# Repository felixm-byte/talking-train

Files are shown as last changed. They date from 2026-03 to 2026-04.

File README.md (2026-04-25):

# talking-train
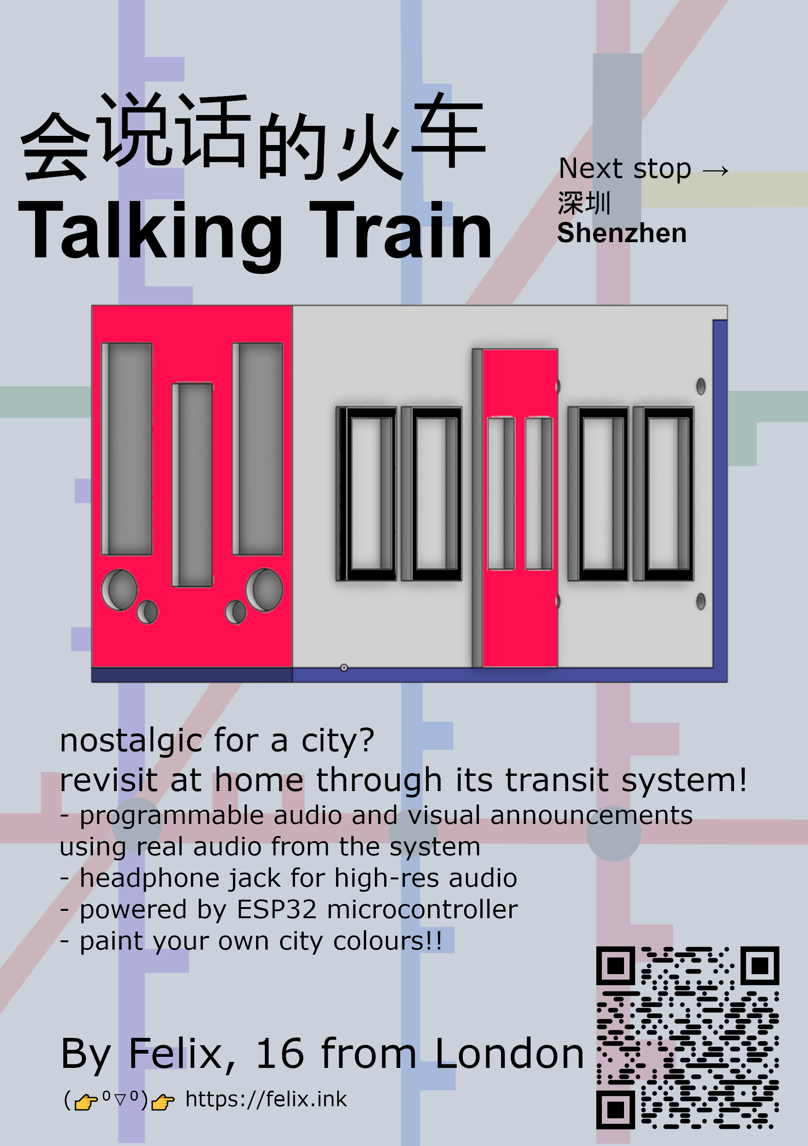
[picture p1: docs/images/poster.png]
poster describing features of the talking train, with a features list and 3D model resembling a London Underground train


This is a bit of an odd concept, but I want to make a talking model train for my grandparents to remind them of their times visiting us, since they are too old to ever make the 19,000 km journey from New Zealand to England. Every time I call them from the train, they light up at the familiarity of the announcements when they hear them and get super nostalgic, which makes me think it would be nice—and a cool souvenir—to let them hear them whenever they like. Technically, I think it would be a cool project, since I’ve never made something with a physical interface, or really made something with hardware, and I would love to learn. Most of what I build would be applicable to other countries, so I think it would be something lots of people would like.

## File structure
- Please ignore /hardware/old-design, for reference only
- Manufacturing files in hardware/manufacturing-outputs/...
- Code in /software - these scripts are in MicroPython and target the ESP32 microcontroller, expecting a 128x64 SSD1306 I2C OLED display and an [I2S audio output device](https://github.com/miketeachman/micropython-i2s-examples)
## Part examples
- SSD1306 128x64 display: https://www.aliexpress.com/item/1005007551771400.html
- Check Bill of Materials file for all other parts, these have LSCS part numbers for ease of ordering
- 4x M2 screws with nuts, 1.4cm length - https://www.aliexpress.com/item/1005006328031034.html (M2x14mm needed)

## Features
- Loads stations and displays them in order on the OLED screen
- Audio playback with hi-res audio
- Line creation tool
- Audio playback support

## Key files
- hardware/manufacturing-outputs/ contains the files (.stl, pick and place, gerber, BOM) needed to produce the finished product, with the 3D files for the case in manufacturing-outputs/3d/ and the PCB in manufacturing-outputs/pcb/ 
- Source files like the EasyEDA (.epro) file and the 3D model of the PCB (only really necessary for designing a new case) is in hardware/source-files
- Use [the onshape file](https://cad.onshape.com/documents/c1f604bc7dcb19d0034320b9/w/e582f7a5ec8be5c9c5e2ed68/e/27ea5781da26a9e15f82bfe8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) onshape for the case 3D source, and access an interactive bom on [my website](https://felix.ink/ttrain1)
- software/ contains the line creation tool and the software for the ESP32 to run.

## Assembly
- Assemble the PCB outside of the case by soldering on the parts. Do not attach the display at this stage. 
- To protect from the unlikely event of soldering error, do not plug the usb-c port directly into an important device: plug into a wall outlet first and check if the power LED is active. If not, I recommend stopping using the device.
- Place this 3D printed piece flat on an assembly bench.
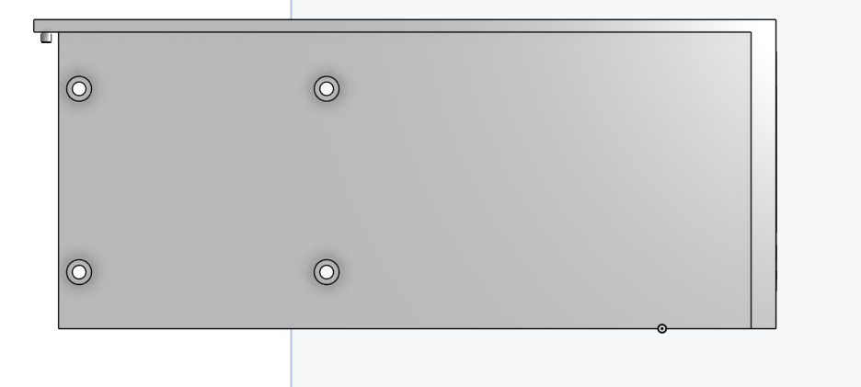
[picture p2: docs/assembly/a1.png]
part with round screw holes pointing out

- Place the PCB onto the round pieces that poke out, which are used to seperate it from the case. Make sure it is in this alignment and that the screwholes line up.
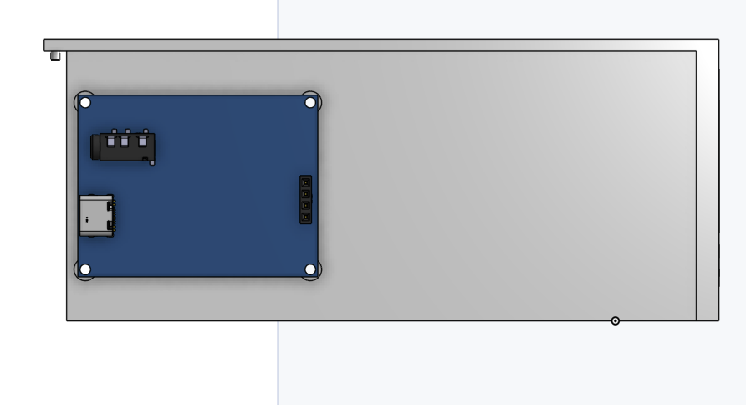
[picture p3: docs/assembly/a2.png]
PCB aligned with scewholes

- Then, insert the screws into the screwholes as shown in the graphic, taking care not to poke the board components.

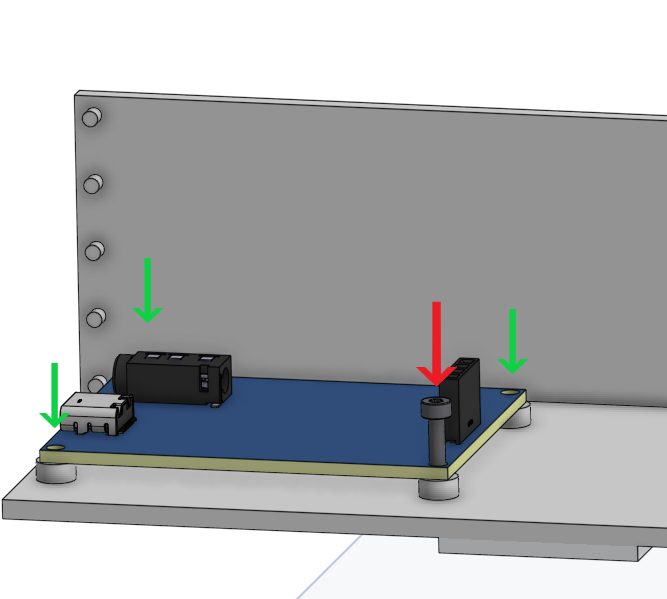
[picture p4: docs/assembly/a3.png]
Inserting screws

- Rotate the model so that it sits with the side of the train on the desk and the top of the train facing upwards. Turn the nut around the screw to secure the PCB.

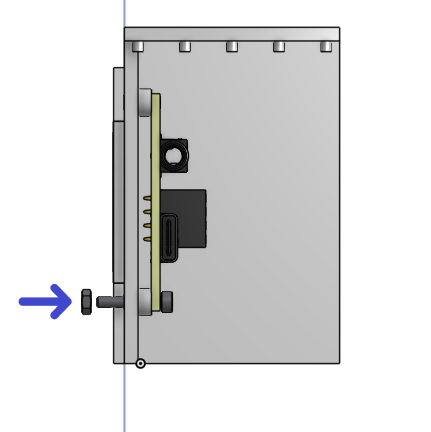
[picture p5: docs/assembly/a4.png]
Securing with nuts

- Next, return the PCB to the original orientation, with the side of the model the PCB is attached to, resting on the desk. Gently attach the display in this orientation, ensuring the pins line up with the header.

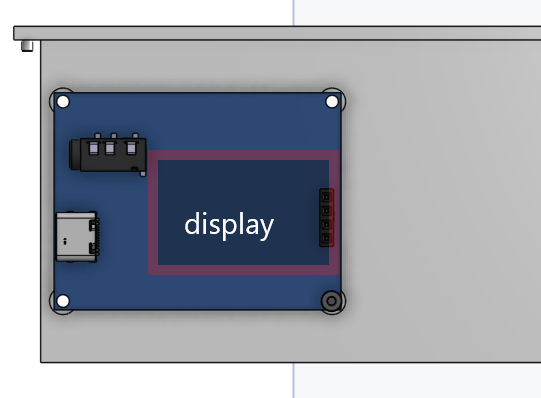
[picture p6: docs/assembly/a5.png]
Orientation for display

- Finally, take the other part of the 3D model, place it down with its base on the desk. Align the attachment pins from the top side (which we have just assembled) with the sockets from the part we put down, and push it in.

This should now be ready for use. Attach by USB-C to your computer, [set up MicroPython](https://docs.sunfounder.com/projects/esp32-starter-kit/en/latest/micropython/python_start/install_micropython.html), flash the software, and attach a pair of wired headphones to the device. 

Note: please be careful with audio - I don't know how loud it'll be until I test the model.

### For reference, other parts rendered:

The pieces used for mounting the top half of the model:
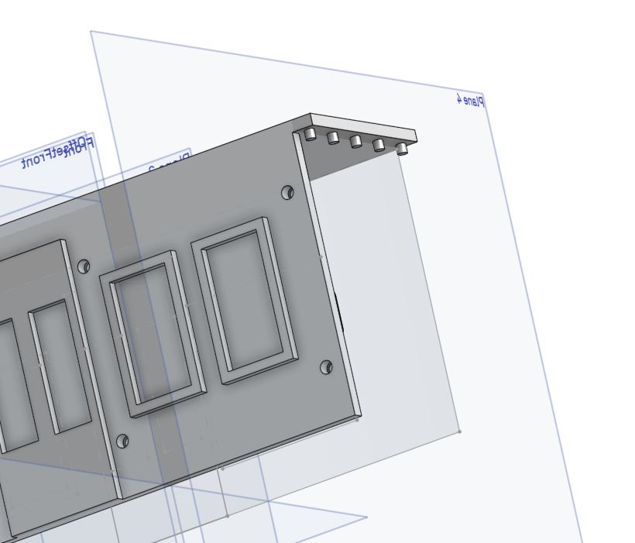
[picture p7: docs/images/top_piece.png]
render of top piece


Fit into these holes on the bottom part of the model.
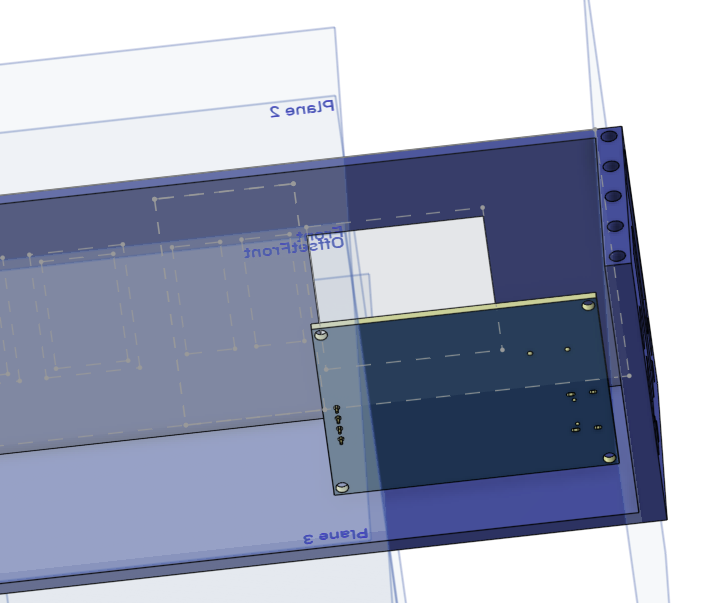
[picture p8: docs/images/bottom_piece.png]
render of bottom piece

## Graphics
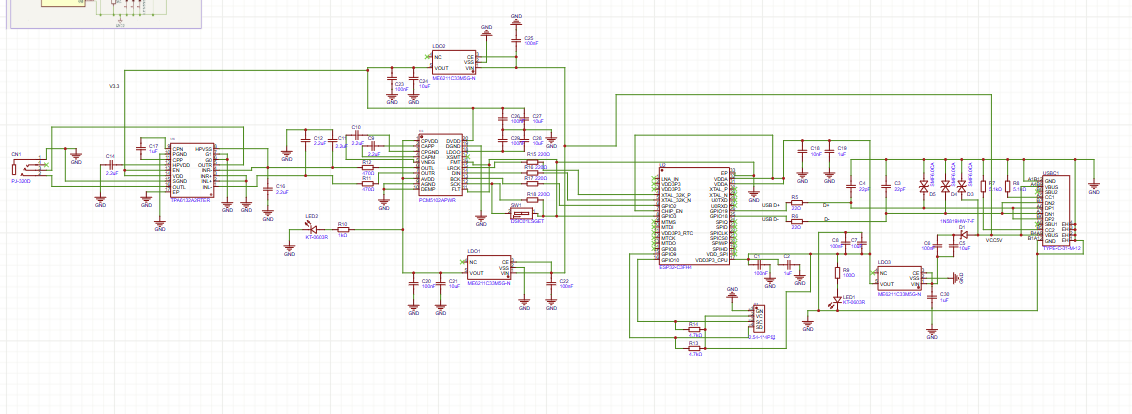
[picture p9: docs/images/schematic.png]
schematic

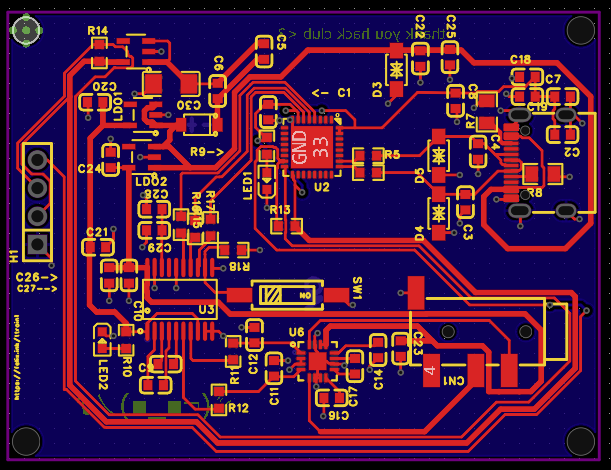
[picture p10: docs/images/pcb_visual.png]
PCB diagram (wiring)

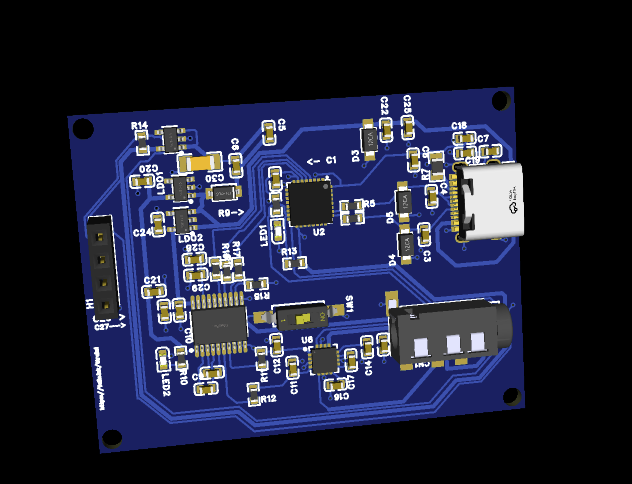
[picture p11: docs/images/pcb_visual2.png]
 - old PCB, for shape reference only
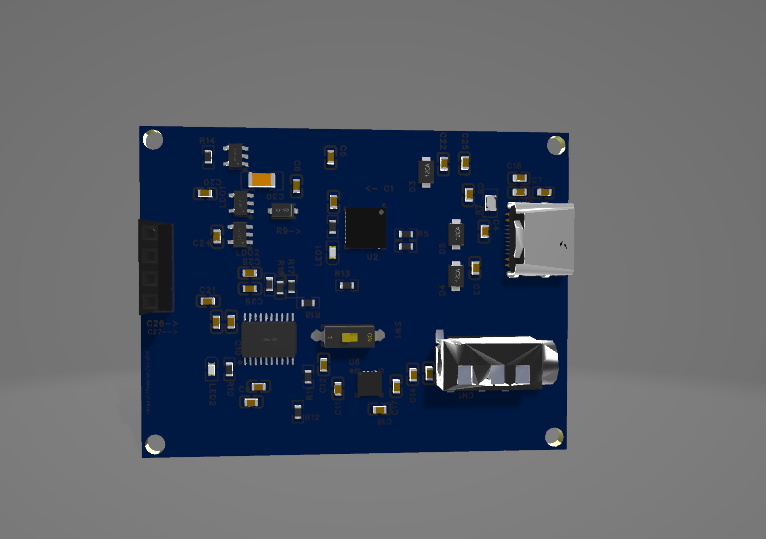
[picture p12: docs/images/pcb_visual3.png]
- old PCB, for shape reference only
## Reference materials
- https://macsbug.wordpress.com/2021/02/19/web-radio-of-m5stack-pcm5102a-i2s-dac/ for DAC schematic
- https://documentation.espressif.com/esp32-c3_datasheet_en.pdf for ESP32-C3 datasheet
- https://www.ti.com/lit/ds/symlink/tpa6132a2.pdf, especially Figure 24, for amplifier datasheet and schematic

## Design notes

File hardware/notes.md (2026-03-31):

The voltage regulator needs to be able to deal with the level of current drawn by the circuit. So, the standard AMS1117-3.3 is insufficient.

# Scale
## Dimensions of PCB:
57 mm height
75 mm width
(with tolerances)
## Dimensions of display
27.8mm height
23.5mm width
(this will fit cleanly within the scale of the PCB)

Hence the dimensions of the opening in the front of the train, for simplicity, should be around the dimensions of the PCB, except wider by about 10mm. 
This isn't exactly precision manufacturing and the display doesn't have a flexible/ribbon connector so it's not a good idea to shrink the size of the opening on the side of the train.

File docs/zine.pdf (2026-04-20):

# 会说话的火车

# Talking Train

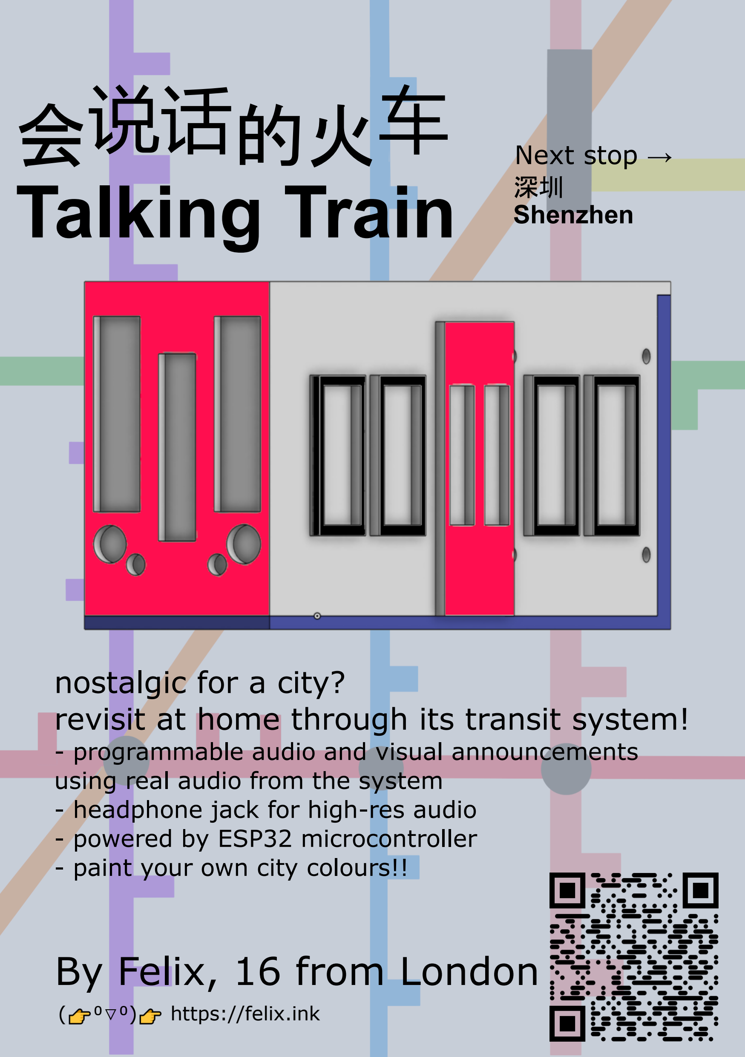
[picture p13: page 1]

深圳
Shenzhen

### nostalgic for a city? revisit at home through its transit system!

- programmable audio and visual announcements using real audio from the system
- headphone jack for high-res audio
- powered by ESP32 microcontroller
- paint your own city colours!!

## By Felix, 16 from London

( ⁰▽⁰) https://felix.ink

Next stop →

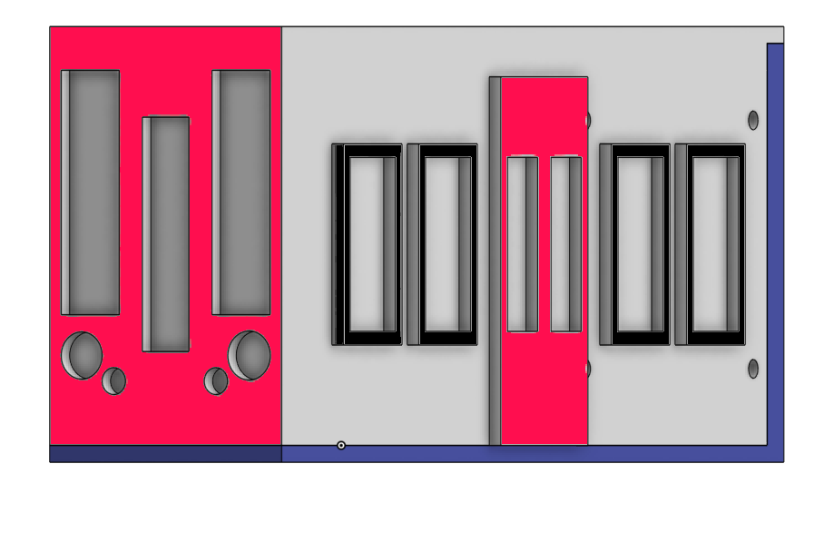
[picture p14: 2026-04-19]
docs/images/model-image.png

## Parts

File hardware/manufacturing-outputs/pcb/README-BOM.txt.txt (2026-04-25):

Access a digital BOM with guidance on part placement on my website at https://felix.ink/ttrain1 (positions are not yet up to date). This has been excluded from the repo to minimise filesize.

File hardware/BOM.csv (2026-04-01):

No. | Quantity | Comment | Designator | Footprint | Value | Manufacturer Part | Manufacturer | Supplier Part | Supplier | JLCPCB Price
1 | 9 | 100nF | C1,C6,C8,C20,C22,C23,C25,C26,C29 | C0603 | 100nF | CC0603KRX7R9BB104 | YAGEO(国巨) | C14663 | LCSC | 0.0005
2 | 3 | 1uF | C2,C17,C19 | C0603 | 1uF | CL10A105KB8NNNC | SAMSUNG(三星) | C15849 | LCSC | 0.0012
3 | 2 | 22pF | C3,C4 | C0603 | 22pF | CL10C220JB8NNNC | SAMSUNG(三星) | C1653 | LCSC | 0.0006
4 | 6 | 10uF | C5,C7,C21,C24,C27,C28 | C0603 | 10uF | CL10A106KP8NNNC | SAMSUNG(三星) | C19702 | LCSC | 0.0012
5 | 6 | 2.2uF | C9,C10,C11,C12,C14,C16 | C0603 | 2.2uF | CL10A225KO8NNNC | SAMSUNG(三星) | C23630 | LCSC | 0.001
6 | 1 | 10nF | C18 | C0603 | 10nF | 0603B103K500NT | FH(风华) | C57112 | LCSC | 0.0005
7 | 1 | 1uF | C30 | C1206 | 1uF | CL31B105KBHNNNE | SAMSUNG(三星) | C1848 | LCSC | 0.0042
8 | 1 | PJ-320D | CN1 | AUDIO-SMD_PJ-320D-1 |  | PJ-320D | SHOU HAN(首韩) | C431535 | LCSC | 0.0077
9 | 1 | 1N5819HW-7-F | D1 | SOD-123_L2.7-W1.6-LS3.7-RD |  | 1N5819HW-7-F | DIODES(美台) | C82544 | LCSC | 0.005
10 | 3 | SMF6.0CA | D3,D4,D5 | SOD-123FL_L2.7-W1.8-LS3.8-BI |  | SMF6.0CA | R+O(宏嘉诚) | C19077500 | LCSC | 0.0045
11 | 1 | 2.54-1*4P母 | H1 | HDR-TH_4P-P2.54-V-F |  | 2.54-1*4P母 | BOOMELE(博穆精密) | C2718488 | LCSC | 0.0112
12 | 3 | ME6211C33M5G-N | LDO1,LDO2,LDO3 | SOT-23-5_L3.0-W1.7-P0.95-LS2.8-BL |  | ME6211C33M5G-N | MICRONE(南京微盟) | C82942 | LCSC | 0.0073
13 | 2 | KT-0603R | LED1,LED2 | LED0603-RD |  | KT-0603R | KENTO | C2286 | LCSC | 0.001
14 | 2 | 22Ω | R5,R6 | R0603 | 22Ω | 0603WAF220JT5E | UNI-ROYAL(厚声) | C23345 | LCSC | 0.0002
15 | 2 | 5.1kΩ | R7,R8 | R0805 | 5.1kΩ | 0805W8F5101T5E | UNI-ROYAL(厚声) | C27834 | LCSC | 0.0004
16 | 1 | 100Ω | R9 | R0603 | 100Ω | 0603WAF1000T5E | UNI-ROYAL(厚声) | C22775 | LCSC | 0.0002
17 | 1 | 1kΩ | R10 | R0603 | 1kΩ | 0603WAF1001T5E | UNI-ROYAL(厚声) | C21190 | LCSC | 0.0003
18 | 2 | 470Ω | R11,R12 | R0603 | 470Ω | 0603WAF4700T5E | UNI-ROYAL(厚声) | C23179 | LCSC | 0.0003
19 | 2 | 4.7kΩ | R13,R14 | R0603 | 4.7kΩ | 0603WAF4701T5E | UNI-ROYAL(厚声) | C23162 | LCSC | 0.0002
20 | 4 | 220Ω | R15,R16,R17,R18 | R0603 | 220Ω | 0603WAF2200T5E | UNI-ROYAL(厚声) | C22962 | LCSC | 0.0002
21 | 1 | DSIC01LSGET | SW1 | SW-SMD_DSIC01LSGET |  | DSIC01LSGET | YE | C54948 | LCSC | 0.0637
22 | 1 | ESP32-C3FH4 | U2 | QFN-32_L5.0-W5.0-P0.50-TL-EP3.7 |  | ESP32-C3FH4 | ESPRESSIF(乐鑫) | C2858491 | LCSC | 0.3472
23 | 1 | PCM5102APWR | U3 | TSSOP-20_L6.5-W4.4-P0.65-LS6.4-BL |  | PCM5102APWR | TI(德州仪器) | C107671 | LCSC | 0.1634
24 | 1 | TPA6132A2RTER | U6 | WQFN-16_L3.0-W3.0-P0.50-TL-EP1.6 |  | TPA6132A2RTER | TI(德州仪器) | C69901 | LCSC | 0.1991
25 | 1 | TYPE-C-31-M-12 | USBC1 | USB-C_SMD-TYPE-C-31-M-12_1 |  | TYPE-C-31-M-12 | 韩国韩荣 | C165948 | LCSC | 0.027
https://www.lcsc.com/

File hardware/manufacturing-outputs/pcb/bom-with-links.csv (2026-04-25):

bom.csv |  |  |  |  |  |  |  |  |  | LCSC BOM Quotation
 |  |  |  |  |  |  |  |  |  | BOM Date Created?25/04/26 21:10:33 |  |  |  | BOM Export Date: 25/04/26 21:10:59 |  |  |  | The matching result is a real-time query result, availability and prices may fluctuate. Backorder items are estimated prices for your reference, please submit "Create Quote" to get the real price. All information is provided "as is" and is subject to change without notice. Any use made of the information provided is without recourse to LCSC and at the user's risk.
 |  |  |  |  |  |  |  |  |  | EST TOTAL :$13.22 |  |  |  | Website?https://www.lcsc.com/bom
Uploaded data |  |  |  |  |  |  |  |  |  | LCSC Matching Results
LCSC# | Mfr. | Mrf# | Description | Package | Value | Customer Part Number | Quantity | Target Price(USD) | Target Lead Time(Business Days) | Mrf# | Mfr. | Order Qty. | Unit Price(USD) | Ext.Price(USD) | LCSC# | Package | Min | Mult | SPQ | Availability | Stock Status | Customer Notes | Description | Matched status | Product Link
C14663,100nF |  |  |  | 0603 |  | - | 9 |  |  | CC0603KRX7R9BB104 | YAGEO | 100 | 0.0030 | 0.30 | C14663 | 0603 | 100 | 100 | 4000 | 4000 | In Stock |  | 100nF ±10% 50V Ceramic Capacitor X7R 0603 | Partial Matches | https://www.lcsc.com/product-detail/C14663.html
C15849,1uF |  |  |  | 0603 |  | - | 3 |  |  | CL10A105KB8NNNC | Samsung Electro-Mechanics | 50 | 0.0078 | 0.39 | C15849 | 0603 | 50 | 50 | 4000 | 291950 | In Stock |  | 1uF ±10% 50V Ceramic Capacitor X5R 0603 | Partial Matches | https://www.lcsc.com/product-detail/C15849.html
C1653,22pF |  |  |  | 0603 |  | - | 2 |  |  | CL10C220JB8NNNC | Samsung Electro-Mechanics | 100 | 0.0036 | 0.36 | C1653 | 0603 | 100 | 100 | 4000 | 3169100 | In Stock |  | 22pF ±5% 50V Ceramic Capacitor C0G 0603 | Partial Matches | https://www.lcsc.com/product-detail/C1653.html
C19702,10uF |  |  |  | 0603 |  | - | 6 |  |  | CL10A106KP8NNNC | Samsung Electro-Mechanics | 50 | 0.0080 | 0.40 | C19702 | 0603 | 50 | 50 | 4000 | 3393500 | In Stock |  | 10uF ±10% 10V Ceramic Capacitor X5R 0603 | Partial Matches | https://www.lcsc.com/product-detail/C19702.html
C23630,2.2uF |  |  |  | 0603 |  | - | 6 |  |  | CL10A225KO8NNNC | Samsung Electro-Mechanics | 50 | 0.0063 | 0.32 | C23630 | 0603 | 50 | 50 | 4000 | 2373850 | In Stock |  | 2.2uF ±10% 16V Ceramic Capacitor X5R 0603 | Partial Matches | https://www.lcsc.com/product-detail/C23630.html
C57112,10nF |  |  |  | 0603 |  | - | 1 |  |  | 0603B103K500NT | FH | 100 | 0.0030 | 0.30 | C57112 | 0603 | 100 | 100 | 4000 | 1412600 | In Stock |  | 10nF ±10% 50V Ceramic Capacitor X7R 0603 | Partial Matches | https://www.lcsc.com/product-detail/C57112.html
C431535,undefined |  |  |  | SMD |  | - | 1 |  |  | PJ-320D | SHOU HAN | 10 | 0.0504 | 0.50 | C431535 | SMD | 10 | 10 | 1000 | 65280 | In Stock |  | 3.5mm Headphone Jack 0.5A 30V Surface Mount | Partial Matches | https://www.lcsc.com/product-detail/C431535.html
C82544,undefined |  |  |  | SOD-123 |  | - | 1 |  |  | 1N5819HW-7-F | DIODES | 20 | 0.0335 | 0.67 | C82544 | SOD-123 | 20 | 20 | 3000 | 205680 | In Stock |  | 40V 1 Independent 450mV@1A 1A SOD-123 Single Diodes RoHS | Partial Matches | https://www.lcsc.com/product-detail/C82544.html
C19077500,undefined |  |  |  | SOD-123FL |  | - | 3 |  |  | SMF6.0CA | R+O | 20 | 0.0308 | 0.62 | C19077500 | SOD-123FL | 20 | 20 | 3000 | 750000 | In Stock |  | 10.3VC Clamp 19.4A@10/1000us Ipp TVS DIODE SOD-123FL | Partial Matches | https://www.lcsc.com/product-detail/C19077500.html
C82942,undefined |  |  |  | SOT-23-5 |  | - | 3 |  |  | ME6211C33M5G-N | MICRONE | 10 | 0.0497 | 0.50 | C82942 | SOT-23-5 | 10 | 10 | 3000 | 164670 | In Stock |  | 3.3V Positive Fixed SOT-23-5 Voltage Regulators - Linear, Low Drop Out (LDO) Regulators RoHS | Partial Matches | https://www.lcsc.com/product-detail/C82942.html
C23345,22? |  |  |  | 0603 |  | - | 2 |  |  | 0603WAF220JT5E | UNI-ROYAL | 100 | 0.0016 | 0.16 | C23345 | 0603 | 100 | 100 | 5000 | 861900 | In Stock |  | 22? ±1% 100mW 0603 Thick Film Resistor | Partial Matches | https://www.lcsc.com/product-detail/C23345.html
C22775,100? |  |  |  | 0603 |  | - | 1 |  |  | 0603WAF1000T5E | UNI-ROYAL | 100 | 0.0019 | 0.19 | C22775 | 0603 | 100 | 100 | 5000 | 0 | Backordered |  | 100? ±1% 100mW 0603 Thick Film Resistor | Partial Matches | https://www.lcsc.com/product-detail/C22775.html
C21190,1k? |  |  |  | 0603 |  | - | 1 |  |  | 0603WAF1001T5E | UNI-ROYAL | 100 | 0.0016 | 0.16 | C21190 | 0603 | 100 | 100 | 5000 | 0 | Backordered |  | 1k? ±1% 100mW 0603 Thick Film Resistor | Partial Matches | https://www.lcsc.com/product-detail/C21190.html
C23179,470? |  |  |  | 0603 |  | - | 2 |  |  | 0603WAF4700T5E | UNI-ROYAL | 100 | 0.0017 | 0.17 | C23179 | 0603 | 100 | 100 | 5000 | 814900 | In Stock |  | 470? ±1% 100mW 0603 Thick Film Resistor | Partial Matches | https://www.lcsc.com/product-detail/C23179.html
C23162,4.7k? |  |  |  | 0603 |  | - | 2 |  |  | 0603WAF4701T5E | UNI-ROYAL | 100 | 0.0014 | 0.14 | C23162 | 0603 | 100 | 100 | 5000 | 1398100 | In Stock |  | 4.7k? ±1% 100mW 0603 Thick Film Resistor | Partial Matches | https://www.lcsc.com/product-detail/C23162.html
C22962,220? |  |  |  | 0603 |  | - | 4 |  |  | 0603WAF2200T5E | UNI-ROYAL | 100 | 0.0015 | 0.15 | C22962 | 0603 | 100 | 100 | 5000 | 424600 | In Stock |  | 220? ±1% 100mW 0603 Thick Film Resistor | Partial Matches | https://www.lcsc.com/product-detail/C22962.html
C54948,undefined |  |  |  | SMD |  | - | 1 |  |  | DSIC01LSGET | YE | 1 | 0.4340 | 0.43 | C54948 | SMD | 1 | 1 | 1000 | 0 | Backordered |  | Dip Switch SPST 1 Position Surface Mount,2.5x6mm Slide, Rocked | Partial Matches | https://www.lcsc.com/product-detail/C54948.html
C2858491,undefined |  |  |  | QFN-32-EP(5x5) |  | - | 1 |  |  | ESP32-C3FH4 | ESPRESSIF | 1 | 2.3340 | 2.33 | C2858491 | QFN-32-EP(5x5) | 1 | 1 | 5000 | 5686 | In Stock |  | QFN-32-EP(5x5) RF Transceiver Modules and Modems RoHS | Partial Matches | https://www.lcsc.com/product-detail/C2858491.html
C107671,undefined |  |  |  | TSSOP-20 |  | - | 1 |  |  | PCM5102APWR | TI | 1 | 1.0200 | 1.02 | C107671 | TSSOP-20 | 1 | 1 | 2000 | 7444 | In Stock |  | 50MHz 2 I2S 1.8V~3.3V TSSOP-20 ADCs/DACs - Special Purpose RoHS | Partial Matches | https://www.lcsc.com/product-detail/C107671.html
C69901,undefined |  |  |  | WQFN-16-EP(3x3) |  | - | 1 |  |  | TPA6132A2RTER | TI | 1 | 1.2685 | 1.27 | C69901 | WQFN-16-EP(3x3) | 1 | 1 | 3000 | 3833 | In Stock |  | 2.1mA 2-Channel 25mWx2@16? Class AB WQFN-16-EP(3x3) Audio Amplifiers RoHS | Partial Matches | https://www.lcsc.com/product-detail/C69901.html
C165948,undefined |  |  |  | SMD |  | - | 1 |  |  | TYPE-C-31-M-12 | Korean Hroparts Elec | 5 | 0.1702 | 0.85 | C165948 | SMD | 5 | 5 | 1000 | 316300 | In Stock |  | USB-C (USB TYPE-C) Receptacle Connector 16 Position Surface Mount | Partial Matches | https://www.lcsc.com/product-detail/C165948.html
C2718488,undefined |  |  |  | ??,P=2.54mm |  | - | 1 |  |  | 2.54-1*4P | BOOMELE(Boom Precision Elec) | 10 | 0.0773 | 0.77 | C2718488 | Through Hole,P=2.54mm | 10 | 10 | 1000 | 181600 | In Stock |  | Female Header 4 Position 2.54mm Pitch Single Row Through Hole -40?~+105? | Partial Matches | https://www.lcsc.com/product-detail/C2718488.html
C1848,1uF |  |  |  | 1206 |  | - | 1 |  |  | CL31B105KBHNNNE | Samsung Electro-Mechanics | 10 | 0.0283 | 0.28 | C1848 | 1206 | 10 | 10 | 2000 | 373070 | In Stock |  | 1uF ±10% 50V Ceramic Capacitor X7R 1206 | Partial Matches | https://www.lcsc.com/product-detail/C1848.html
C2286,undefined |  |  |  | 0603 |  | - | 2 |  |  | KT-0603R | Hubei KENTO Elec | 100 | 0.0067 | 0.67 | C2286 | 0603 | 100 | 100 | 4000 | 4156800 | In Stock |  | Red 645nm LED Indication - Discrete 2.4V 0603 | Partial Matches | https://www.lcsc.com/product-detail/C2286.html
C27834,5.1k? |  |  |  | 0805 |  | - | 2 |  |  | 0805W8F5101T5E | UNI-ROYAL | 100 | 0.0027 | 0.27 | C27834 | 0805 | 100 | 100 | 5000 | 5741400 | In Stock |  | 5.1k? ±1% 125mW 0805 Thick Film Resistor | Partial Matches | https://www.lcsc.com/product-detail/C27834.html

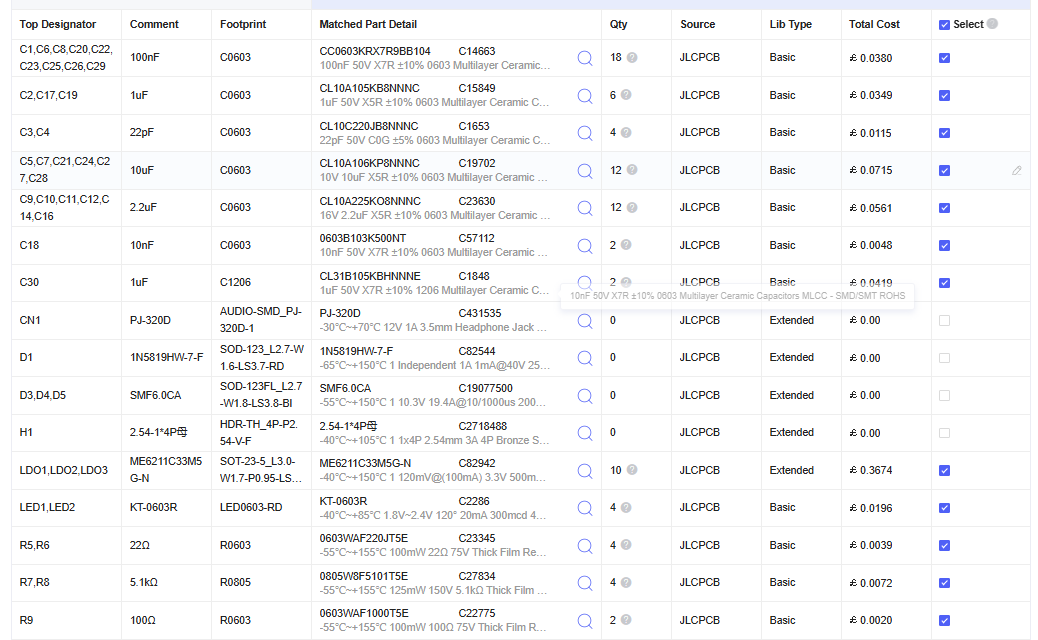
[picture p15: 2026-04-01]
hardware/parts-skipped.png

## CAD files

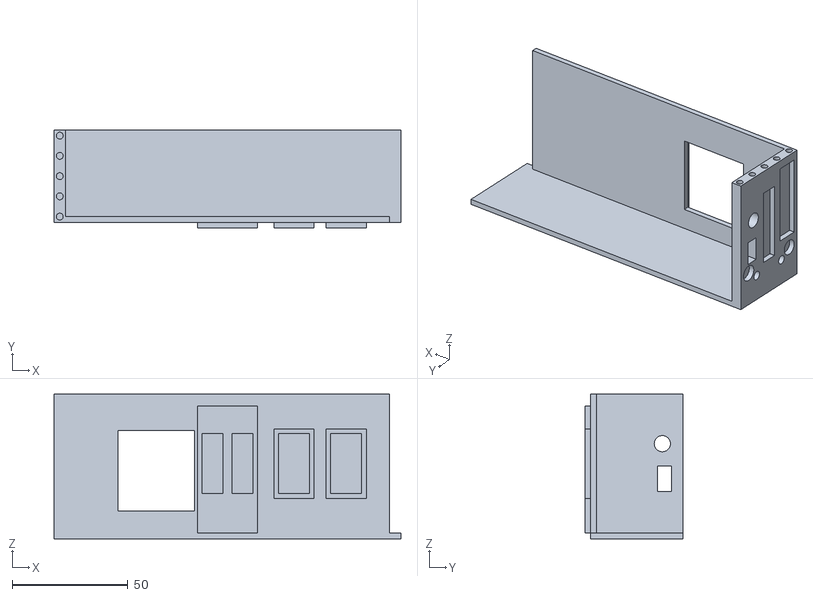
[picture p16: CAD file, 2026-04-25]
hardware/manufacturing-outputs/3d/part_1.stl
150.0 x 42.5 x 62.5

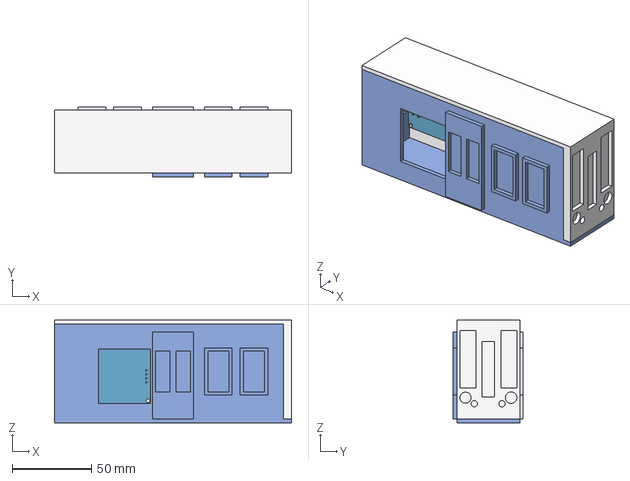
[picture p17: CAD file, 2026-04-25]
hardware/source-files/3d-model/model-source.step
150.0 x 44.5 x 65.0 mm

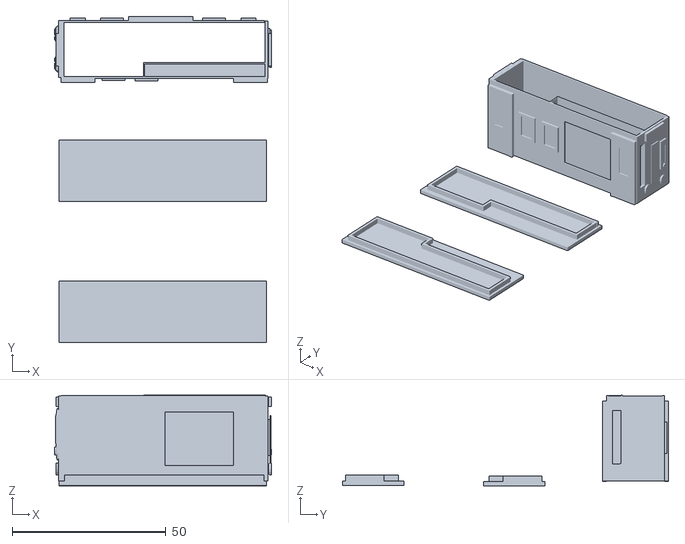
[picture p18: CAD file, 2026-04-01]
hardware/tubetrain-stretched.stl
70.5 x 106.0 x 29.5

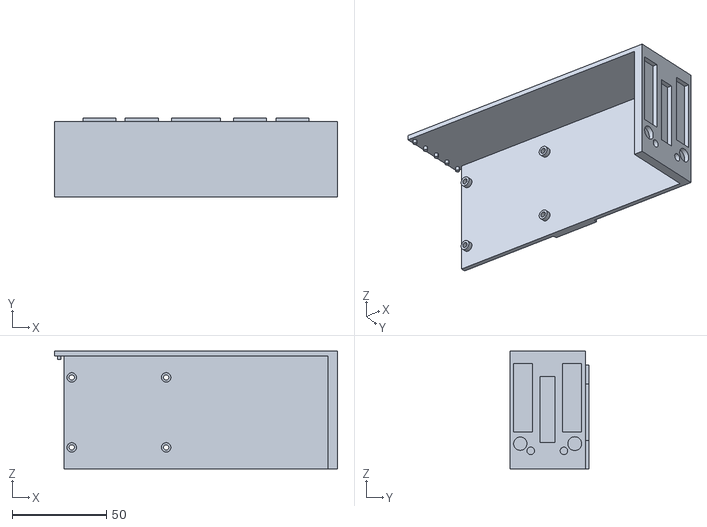
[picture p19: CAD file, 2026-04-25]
hardware/manufacturing-outputs/3d/part_2.stl
150.0 x 42.0 x 62.5

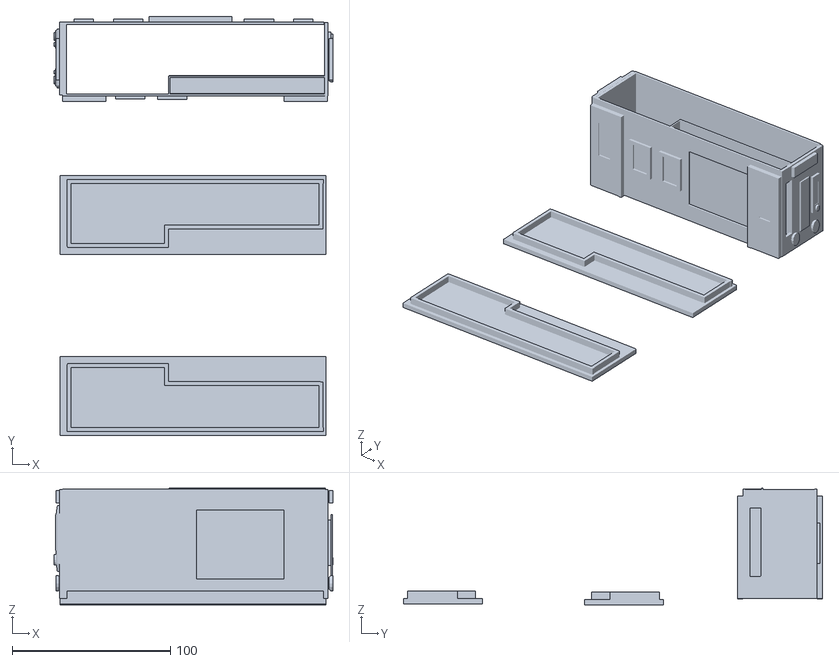
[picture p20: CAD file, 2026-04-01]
hardware/working-model.stl
176.2 x 265.0 x 73.8

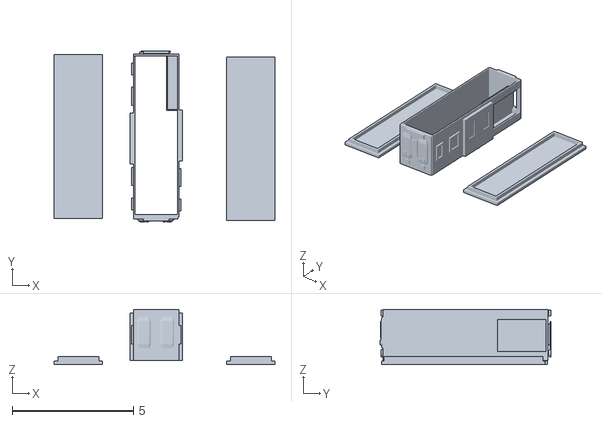
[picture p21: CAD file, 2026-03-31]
hardware/tubetrain-310326.stl
9.10 x 7.05 x 2.27

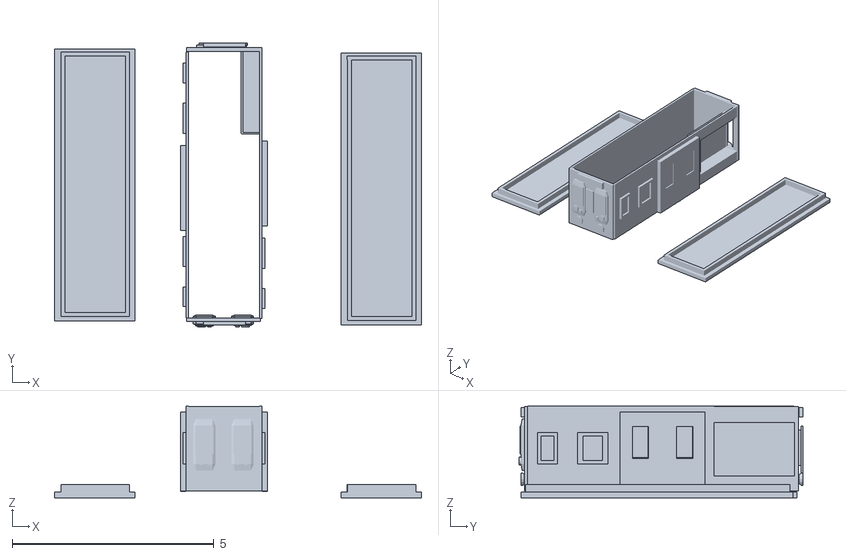
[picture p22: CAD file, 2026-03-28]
hardware/tubetrain-cyd.stl
9.10 x 7.05 x 2.27

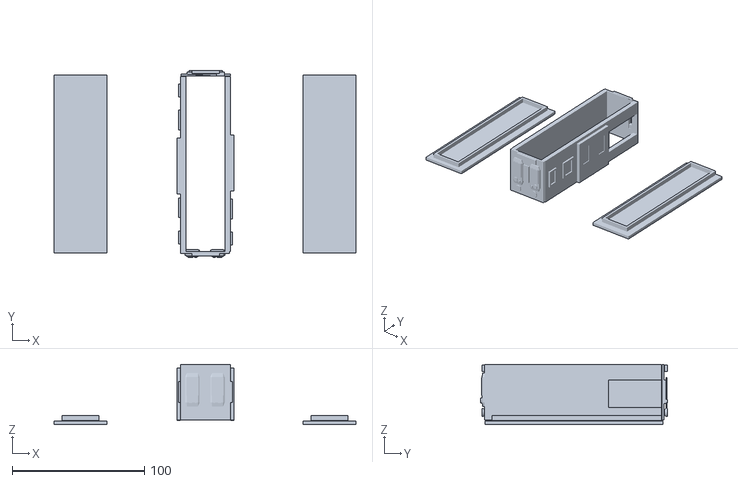
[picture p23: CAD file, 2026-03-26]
hardware/tubetrain_optimised.stl
228.0 x 141.0 x 45.4

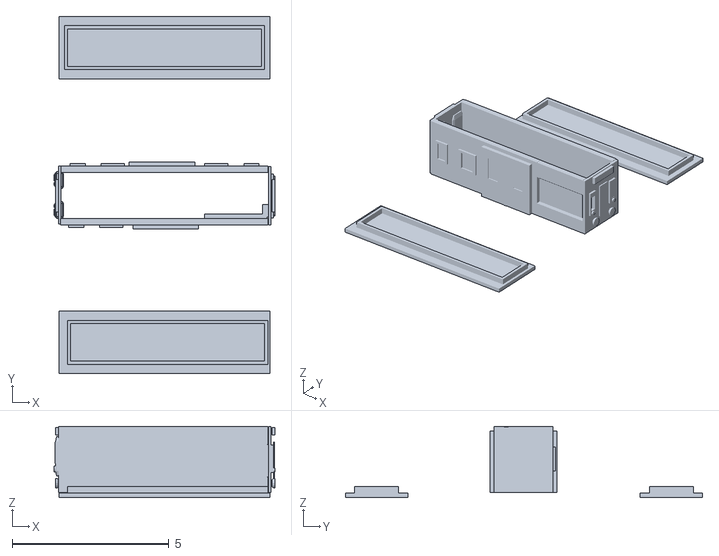
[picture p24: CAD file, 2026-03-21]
hardware/tubetrain.stl
7.05 x 11.4 x 2.27

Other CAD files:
hardware/talking-train.obj
hardware/old-design/talking-train.obj

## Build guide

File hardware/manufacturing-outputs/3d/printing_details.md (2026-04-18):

# Details on 3D printing

- I am using the JLC3DP print service to produce this, which has a cost of about $10 + shipping.
- The models should have roughly these proportions:
15×6.25×4.2 cm
- Access the source files at onshape: https://cad.onshape.com/documents/c1f604bc7dcb19d0034320b9/w/e582f7a5ec8be5c9c5e2ed68/e/27ea5781da26a9e15f82bfe8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
- They are intended to be painted after printing, so consider this when choosing the colour of material to use.

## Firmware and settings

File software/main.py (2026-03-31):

from machine import Pin, I2C, SDCard, I2S
import ssd1306
import time
import os
#some code based on miketeachman/micropython-i2s-examples

audio_enabled = True #toggle audio for the whole program e.g for testing in wokwi which lacks audio support

#switch_button = Pin(34, Pin.IN) button not in use

#creating I2C controller for SSD1306 OLED display
i2c = I2C(0, scl=Pin(22), sda=Pin(21))
oled_width = 128
oled_height = 64
oled = ssd1306.SSD1306_I2C(oled_width, oled_height, i2c)
audio_playing = False

if audio_enabled: #configure audio pinout and settings if audio is in use
    SCK_PIN = 32
    WS_PIN = 25
    SD_PIN = 33
    I2S_ID = 0
    BUFFER_LENGTH_IN_BYTES = 5000
    WAV_SAMPLE_SIZE_IN_BITS = 32
    FORMAT = I2S.STEREO
    SAMPLE_RATE_IN_HZ = 16000

sd = SDCard(slot=2)  #ESP£2 pins used: sck=18, mosi=23, miso=19, cs=5
os.mount(sd, "/sd")

def play_audio(filepath):
    global audio_playing
    audio_playing = True
    wav = open(filepath, 'rb') #rb used for reading binary file format
    _ = wav.seek(44) # advances to first data piece, after metadata/headers
    wav_samples = bytearray(10000)
    wav_samples_mv = memoryview(wav_samples)
    try:
        while True:
            num_read = wav.readinto(wav_samples_mv)
            # end of WAV file?
            if num_read == 0:
                # end-of-file, documentation uses this command to advance to first byte of Data section:
                #_ = wav.seek(44)#
                #i want to end the output, not jump back to the start
                break
            else:
                _ = audio_out.write(wav_samples_mv[:num_read])
    except Exception as e:
        print(f"Error occured while playing {filepath}")
        print(f"Error details: {e}")
    audio_playing = False
    



def get_line_data(line_name):
    try: 
        file = open(f"{line_name}.lnfile", 'r')
    except Exception:
        file = open(f"jubilee_line.lnfile", 'r')

    txt = file.read()
    data = txt.split("\n")
    data[2] = data[2].split(",")
    return data



def display_line(line_name):
    global audio_enabled
    global audio_playing
    line = get_line_data(line_name)

    for stop in line[2]:
        #data is displayed by the oled.text(a,b,c, d) function 
        #a: text, b: x-coord (width is 128), c: y-coord (height is 64), d: colour option (int)

        oled.text(f"{line[0]} line", 0, 0, 1)#this model only has one colour, this i
        oled.text(f"To: {line[1]}", 0, 15,1)
        oled.text(f"{stop}", 0, 45, 1)   
        oled.show()
        #play 1st part of announcement
        try:
            for audio in line[3]:
                if audio[0] == "*":
                    time.sleep(float(audio[1:]))
                else:
                    play_audio(f"{audio}.wav")
                    audio_playing = True
                    while audio_playing:
                        time.sleep(0.01)
        except:
            pass
        #play next part of announcement, station name
        try:
            play_audio(f"{stop}.wav")
            audio_playing = True
            while audio_playing:
                time.sleep(0.01)
        except:
            pass
        #play final part of announcement
        try:
            for audio in line[4s]:
                if audio[0] == "*":
                    time.sleep(float(audio[1:]))
                else:
                    play_audio(f"{audio}.wav")
                    audio_playing = True
                    while audio_playing:
                        time.sleep(0.01)
        except:
            pass        
        time.sleep(5)
        oled.fill(0)
    
#oled.fill(0)
#oled.text("Display complete.", 0,0,1)
#oled.text("Turn off and on to go again.", 0,25,1)
#oled.show()

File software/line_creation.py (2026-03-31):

# this is in python and not intended to be ran on the microcontroller

def create_line_file(line_name, display_name, stations, audio_before, audio_after):
    line = open(f"{line_name}.lnfile", "w")
    text = f"{display_name} \n{stations[-1]} \n"
    for station in stations:
        text += f"{station} "
    text += "\n"
    for audio in audio_before:
        text += f"{audio} "
    text += "\n"
    for audio in audio_after:
        text += f"{audio} "
    line.write(text)

if 'y' in input("Create a new line? y/n").lower():
    print("If you make any mistakes you can restart the program.")
    line_name = input("Line name (include 'line' if necessary): ")
    file_name = input("File name for the line, in snake_case (no spaces!!): ")
    stations = []
    print("Enter the stations, from start to end, including the terminus.")
    print("Enter 's' to stop inputting stations")
    while True:
        station = input("Station name: ")
        if station.lower() != "s":
            stations.append(station)
        else:
            break
    audio_before = []
    while True:
        audio = input("Name of audio file to play BEFORE station name announcement, enter s to stop, enter *x where x is pause in seconds to pause: ")
        if audio.lower() != "s":
            audio_before.append(audio)
        else:
            break
    audio_after = []
    while True:
        audio = input("Name of audio file to play AFTER station name announcement, enter s to stop, enter *x where x is pause in seconds to pause: ")
        if audio.lower() != "s":
            audio_before.append(audio)
        else:
            break
    create_line_file(file_name, line_name, stations, audio_before, audio_after)

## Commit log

2026-03-26 Optimised 3D model for printing
    [tubetrain_optimised.stl]
2026-03-28 Optimised 3D models and updated Readme
    [tubetrain-cyd.stl]
2026-03-30 Create Bill of Materials (LCSC).xls
    [Bill of Materials (LCSC).xls]
2026-03-31 Docs changes. software improvements, build
    [Drill_NPTH_Through.DRL, Drill_PTH_Through.DRL, Drill_PTH_Through_Via.DRL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]
2026-04-01 Created poster, models
    [tubetrain-stretched.stl, working-model.stl]
2026-04-01 Improved docs, replaced gerber
    [BOM.xlsx, Bill of Materials (LCSC).xls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]
2026-04-18 Updated design, file organisation
    [BOM.csv, BOM.xlsx, part_1.stl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]
2026-04-19 Organised repo, completed design
    [bom.csv, pick-and-place.csv]
2026-04-23 Update BOM guidance with note on part positions
2026-04-25 Documentation, 3D model improvement
    [model-source.step]
2026-04-25 Added links to BOM
    [bom-with-links.csv, part_1.stl, part_2.stl]
